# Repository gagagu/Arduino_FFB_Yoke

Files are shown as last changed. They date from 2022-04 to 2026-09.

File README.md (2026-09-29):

# Arduino_FFB_Yoke
Flightsim FFB Yoke with Arduino Leonardo

## see the fork of my project: 
[here](https://github.com/barsk/Arduino_FFB_Yoke)

### use at your own risk. 
I am not responsible for any damage to man and machine. Be careful when handling electronics and mechanics.

### It is not allowed to use my work in a commercial way!
If you want to use it in an commercial way please contact me.

## Please study the [Wiki](https://github.com/gagagu/Arduino_FFB_Yoke/wiki) for more info and before you begin!

## New Hardware and new PCB Verison 2.0
The new Hardware is using an Arduino Pro Micro instead of original Arduino Micro because it's cheaper and easier to order.
The new Hardware created by JR4 is working with the old PCB V1.3.5 and the new PCB V2.0

The new Hardware is available [here](https://www.thingiverse.com/thing:6464701)

I have done some remixed with different planetary gears and other stuff [here](https://www.thingiverse.com/thing:6786283)

For the new Code with automatic calibration switch the branch to "2.0" but be careful, it's in alpha state and I am not responsible for any damage to man and machine. Be careful when handling electronics and mechanics.

To open the Code in Arduino Studio you have to place it into a directory called "Arduino_FFB_Yoke"!

You can use the code with board v2.0 and board v1.3.5 together. You only have to switch in defines.h file.

### This project is still in development and will be extend constantly.

It shows how to create a force feedback yoke (and later pedals) for using with Flight Simulator.
It consist of 3d components, electronic schematics and arduino source code.

## Discord
You are welcome to join my Discord to get newest Info and support, [here](https://discord.gg/zrYUcJWu7F)

## Ref
This project is a combination of several existing github projects and 3d Models from Thingiverse.com

### Github Projects, Thanks a lot for your work!
* [FINO](https://github.com/jmriego/Fino)
* [Heironimus](https://github.com/MHeironimus/ArduinoJoystickLibrary)
* [hoantv](https://github.com/hoantv/VNWheel)
* [YukMingLaw](https://github.com/YukMingLaw/ArduinoJoystickWithFFBLibrary) 
* [arafin](https://github.com/araffin/arduino-robust-serial/)
* [jimmyberg](https://github.com/jimmyberg/LowPassFilter)

### Thingiverse
* [Arduino FFB Yoke 2.0](https://www.thingiverse.com/thing:6464701)
* [Arduino FFB Yoke 2.0 Remixes](https://www.thingiverse.com/thing:6786283)
* [CadetYoke v2.0](https://www.thingiverse.com/thing:4884092)
* [Saitek FFB Yoke](https://www.thingiverse.com/thing:5241628)

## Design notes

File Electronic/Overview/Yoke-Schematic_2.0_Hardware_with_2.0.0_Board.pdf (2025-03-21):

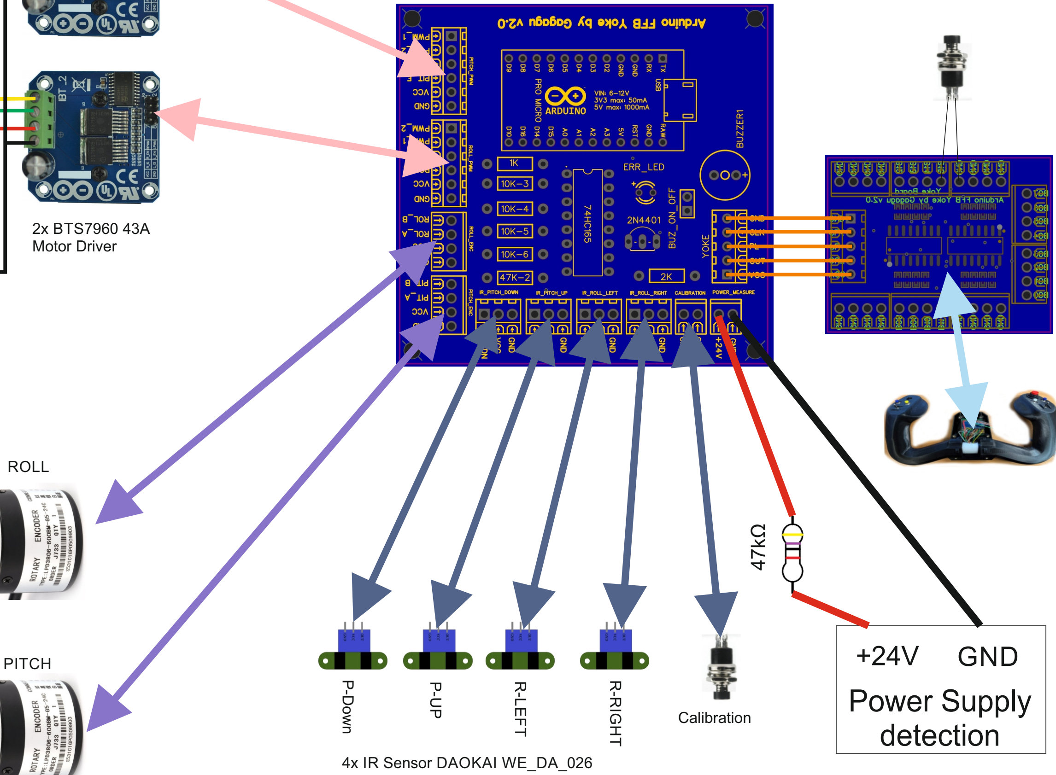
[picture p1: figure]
P-Down; RIG; 4x IR Sensor DAOKAI WE_DA_026; 2x BTS7960 43A Motor Driver; Calibration; ROLL; PITCH; GND; Power Supply detection

Power Supply
24V 10A

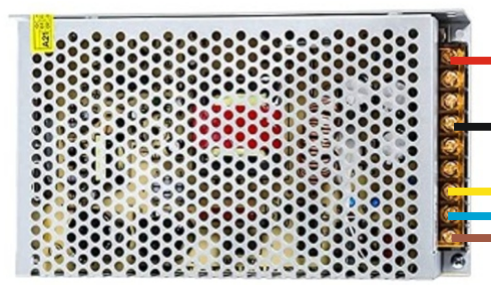
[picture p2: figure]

Power Plug
with Switch

2x 775 DC Motor
12V-36V
3500-900Rpm

# Board v2.0.0 with Hardware 2.0

PITCH

ROLL

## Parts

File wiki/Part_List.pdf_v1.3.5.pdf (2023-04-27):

Partlist Gagagu Arduino FFB Yoke | V1.3 | (prices can change)
Piece | Name | Price Single | Note | Price | Link
1 | Arduino Micro | 19,44 € | | 19,44 € | Link (https://store.arduino.cc/products/arduino-micro)
2 | BTS7960 43A | 15,99 € | Motor Driver Module | 31,98 € | Link (https://www.amazon.de/gp/product/B09FLB44TV)
2 | CD74HC4057 | 8,99 € | Multiplexer | 17,98 € | Link (https://www.amazon.de/gp/product/B07VF14YNG)
2 | 775 DC Motor | 15,59 € | 12V-36V 3500-900Rpm | 31,18 € | Link (https://www.amazon.de/gp/product/B075D85KVV)
10 | WE-DA-026 | 1,52 € | IR Speed Sensor | 15,20 € | Link (https://www.amazon.de/dp/B09TK2H9NY)
1 | HD44780 2004 | 10,00 € | LCD Display 4x20 | 10,00 € | Link (https://www.amazon.de/gp/product/B0822PP3WM)
1 | Power Supply 24V 10A | 25,99 € | | 25,99 € | Link (https://www.amazon.de/gp/product/B09JKJGT4M)
2 | MGN12H | 16,99 € | Linear Guide 200mm | 33,98 € | Link (https://www.amazon.de/gp/product/B093LKT3L9)
2 | HK 2512 | 7,19 € | Ball Bearing 25x32x12 | 14,38 € | Link (https://www.amazon.de/dp/product/B0828XDNJ3)
2 | Aeronaut Shaft Adapter | 5,60 € | No- 712455 | 11,20 € | Link (https://www.amazon.de/gp/product/B013GE06JG)
6 | Button Yoke | 0,40 € | Mini Buttons | 2,40 € | Link (https://www.amazon.de/gp/product/B081TZFZVS)
2 | Switch Yoke | 1,00 € | MTS-123 on-off-on | 2,00 € | Link (https://www.amazon.de/gp/product/B07H5NX4G9)
1 | Button Calibration | 5,99 € | | 5,99 € | Link (https://www.amazon.de/dp/B09BMRDPTN)
1 | Delock USB 2.0 Cable | 7,25 € | 25cm | 7,25 € | Link (https://www.amazon.de/dp/B0754MNQPN)
4 | 20x20L B-Typ Nut6 | 3,28 € | 400mm | 13,12 € | Link (https://www.amazon.de/dp/B09FYFBW1M)
1 | Power Switch | 7,49 € | | 7,49 € | Link (https://www.amazon.de/dp/B01H5MK3OI)
1 | Potentiometer | 6,99 € | 10K | 6,99 € | Link (https://www.amazon.de/gp/product/B0B2ZK6YL6)
1 | Taktile Switche | 10,80 € | 5Way Switch | 10,80 € | Link (https://www.amazon.de/gp/product/B0842K7V2L)
1 | Thread insert | 15,45 € | For Yoke Model | 15,45 € | Link (https://www.amazon.de/gp/product/B09MK3VCYC)
1 | Small Screws | 8,39 € | For Yoke Model | 8,39 € | Link (https://www.amazon.de/gp/product/B093BY1XJJ)
2 | Pushbutton Yoke | 0,50 € | 12mm | 1,00 €
1 | Several Screws, Washers and Nuts | 30,00 € | | 30,00 €
10 | Resistors | 0,25 € | 10K | 2,50 €
1 | Div. Cables | 20,00 € | | 20,00 €
1 | Housing (wood) | 30,00 € | | 30,00 €
1 | Metal Pipe 25mm | 8,00 € | | 8,00 €
1 | ecoPla White | 21,99 € | | 21,99 €
404,70 €

8 | M2.5x8-Screw
10 | M3x10-Screw
8 | M3x12-Screw
4 | M3x14-Screw
8 | M3x16-Screw
20 | M3x20-Screw
4 | M4x20-Screw
8 | M4x25-Screw
1 | M4x35-Screw
8 | M6x20-Screw
12 | M6x25-Screw
6 | M6x30-Screw
4 | M6x50-Screw
50 | M3-Washer
12 | M4-Washer
22 | M6-Washer
22 | M6-Nut
8 | M2.5-Nut
50 | M3-Nut
13 | M4-Nut

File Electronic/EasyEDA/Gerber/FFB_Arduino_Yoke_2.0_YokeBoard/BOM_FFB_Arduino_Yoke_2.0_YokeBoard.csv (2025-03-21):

ID | Name | Designator | Footprint | Quantity | Manufacturer Part | Manufacturer | Supplier | Supplier Part | Price
1 | 10kΩ | R1,R2,R3,R4,R5,R6,R7,R8,R9,R10,R11,R12,R13,R14,R15,R16 | R0603 | 16 | 0603WAF1002T5E | UNI-ROYAL(厚声) | LCSC | C25804 | 0.001
2 | 74HC165D,653 | IC1,IC2 | SOIC-16_L9.9-W3.9-P1.27-LS6.0-BL | 2 | 74HC165D,653 | Nexperia(安世) | LCSC | C5613 | 0.111

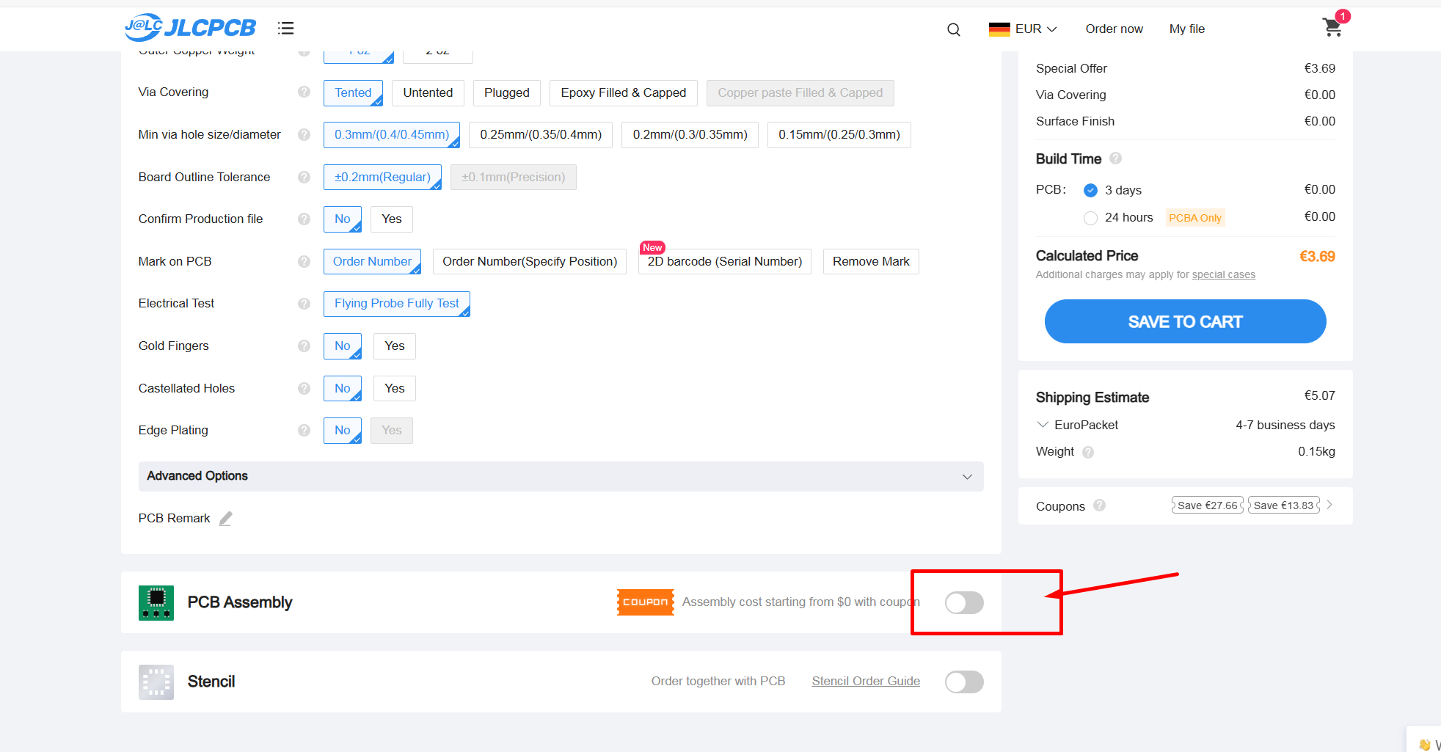
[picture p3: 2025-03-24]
Images/PCB_Order/Order_06.png

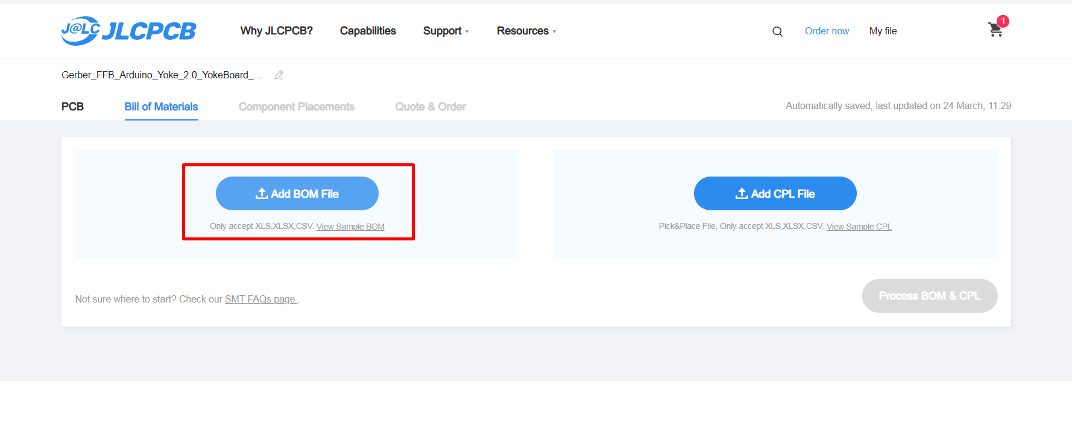
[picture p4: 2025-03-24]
Images/PCB_Order/Order_09.png

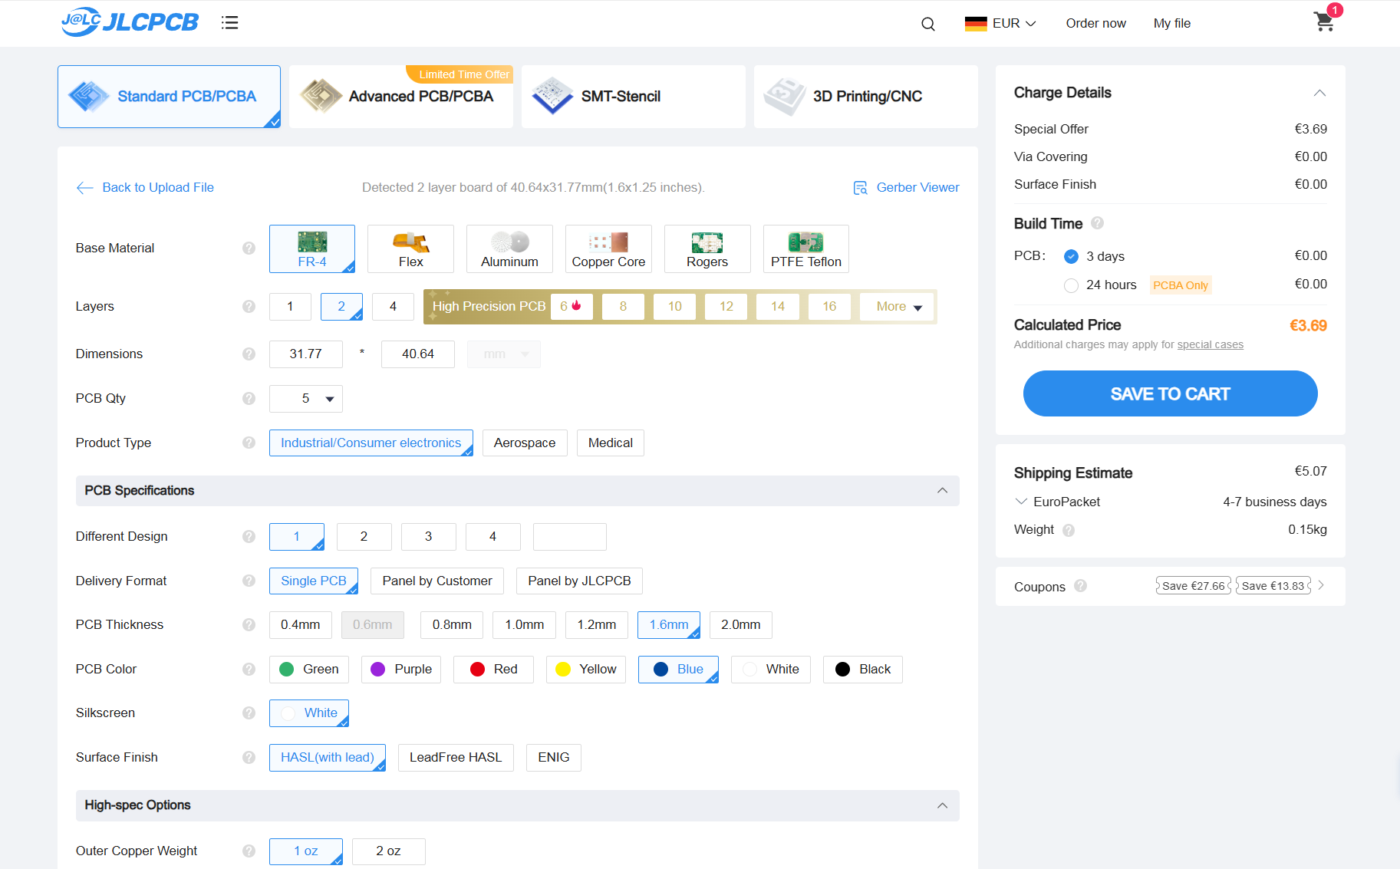
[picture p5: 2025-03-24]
Images/PCB_Order/Order_05.png

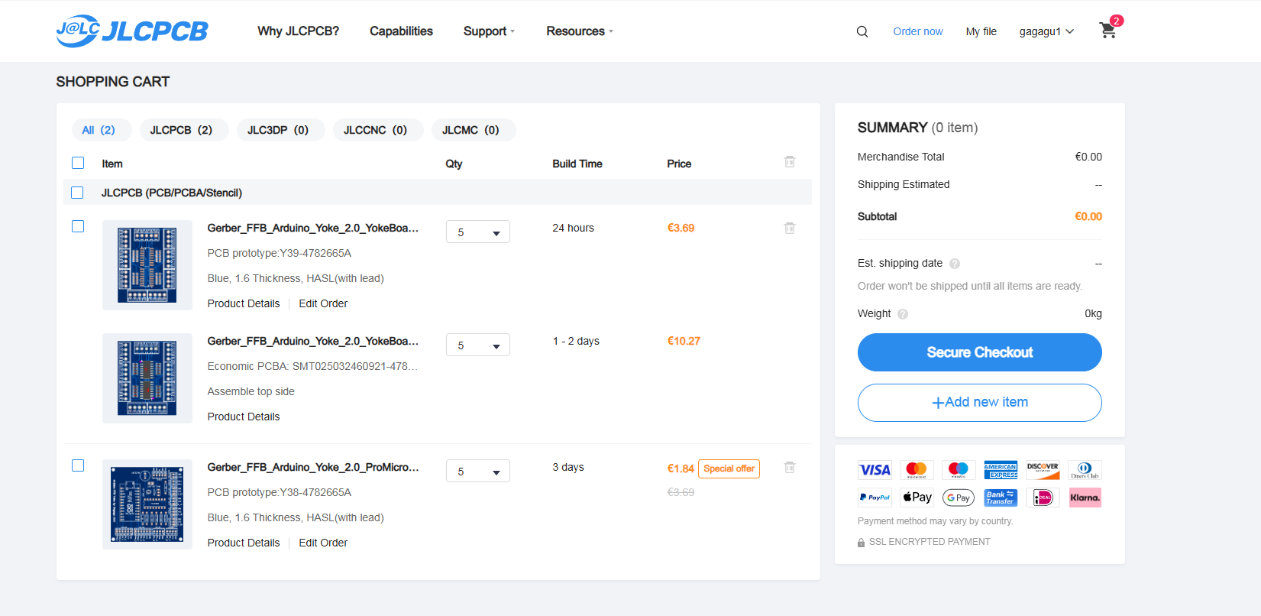
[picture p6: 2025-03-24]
Images/PCB_Order/Order_15.png

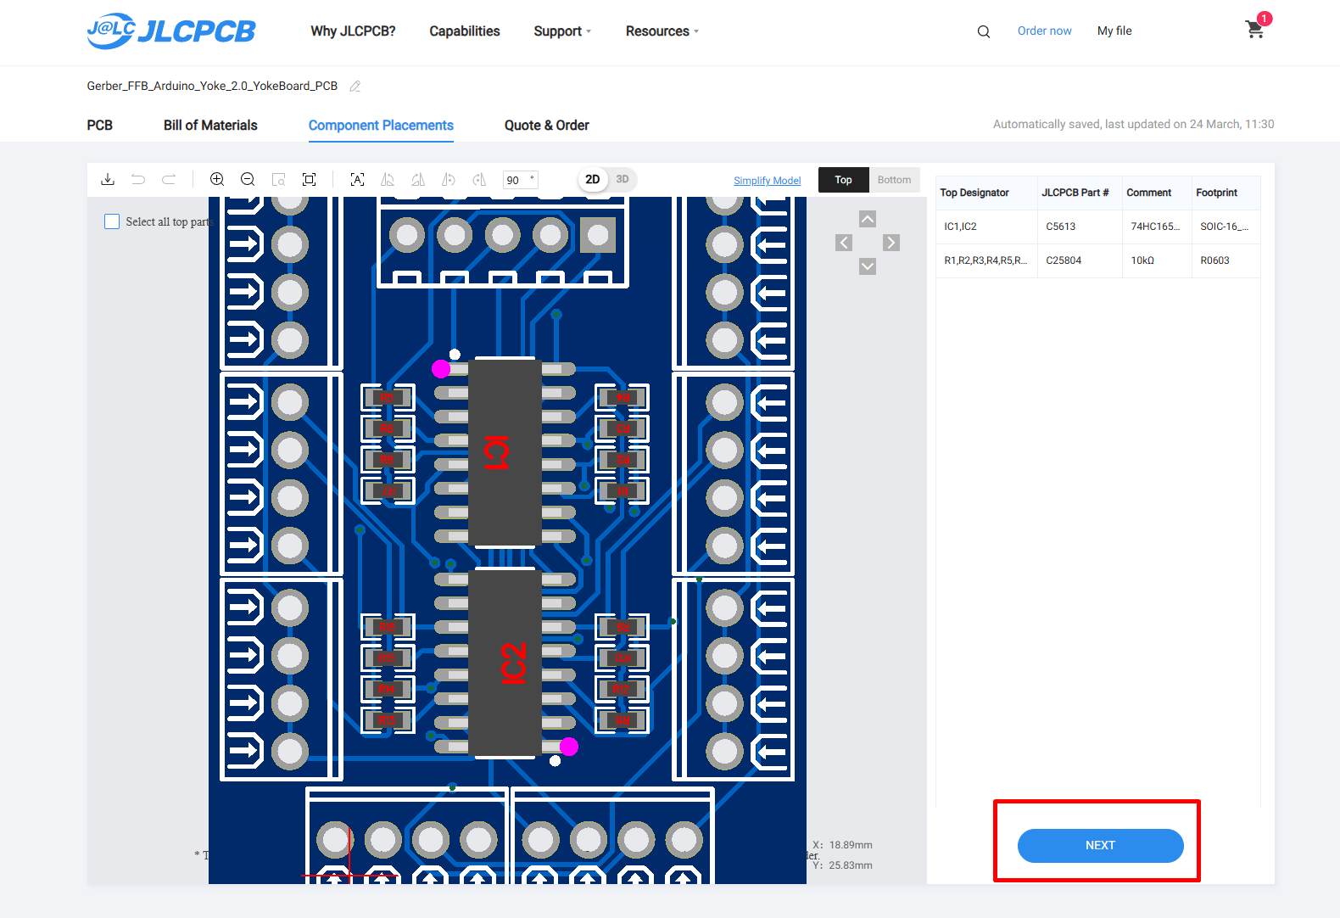
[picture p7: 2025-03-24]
Images/PCB_Order/Order_13.png

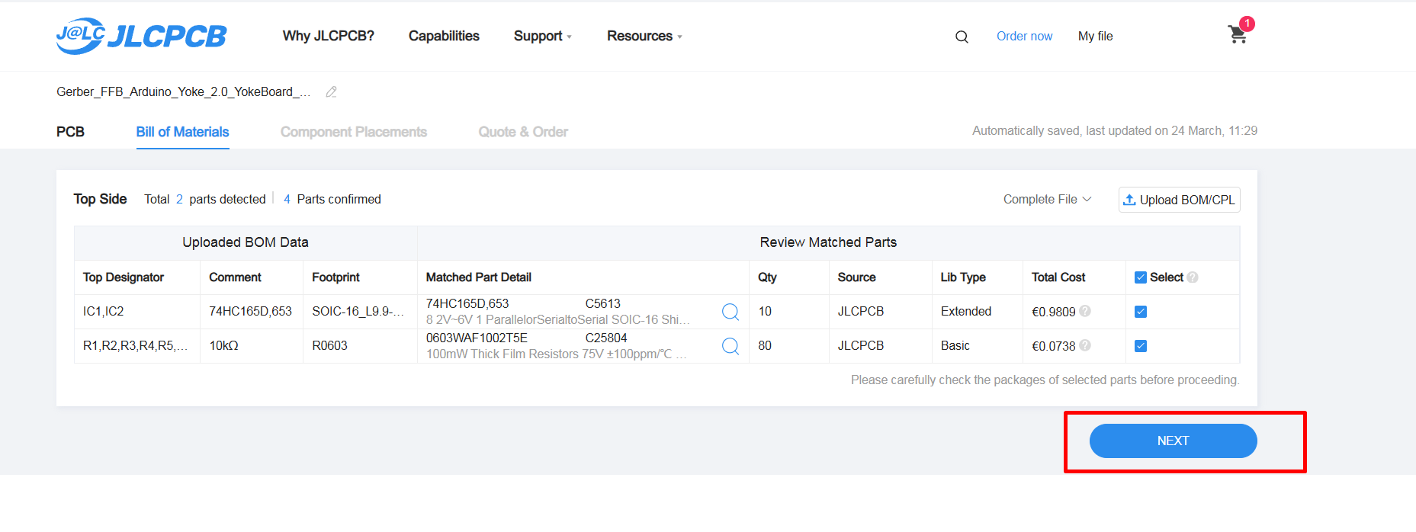
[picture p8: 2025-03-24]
Images/PCB_Order/Order_12.png

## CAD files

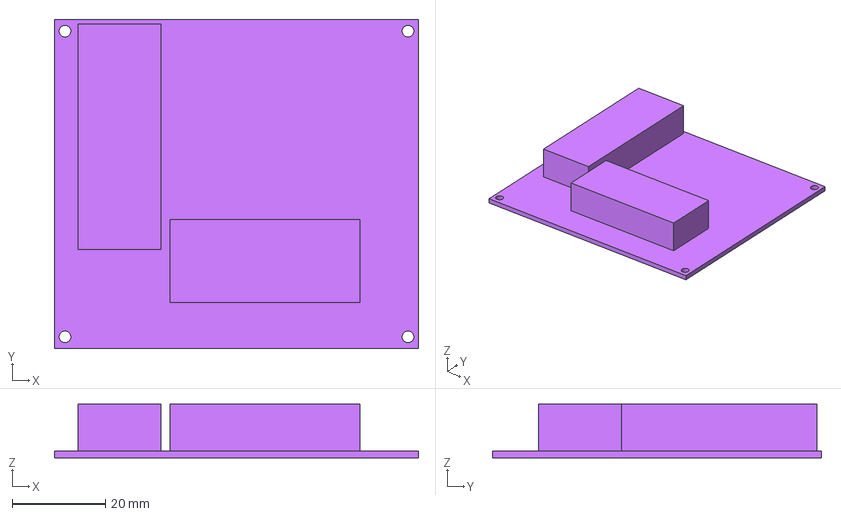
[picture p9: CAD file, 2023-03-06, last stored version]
Cad/FreeCad/Electronics/Mainboard.FCStd
78.0 x 70.5 x 11.5 mm

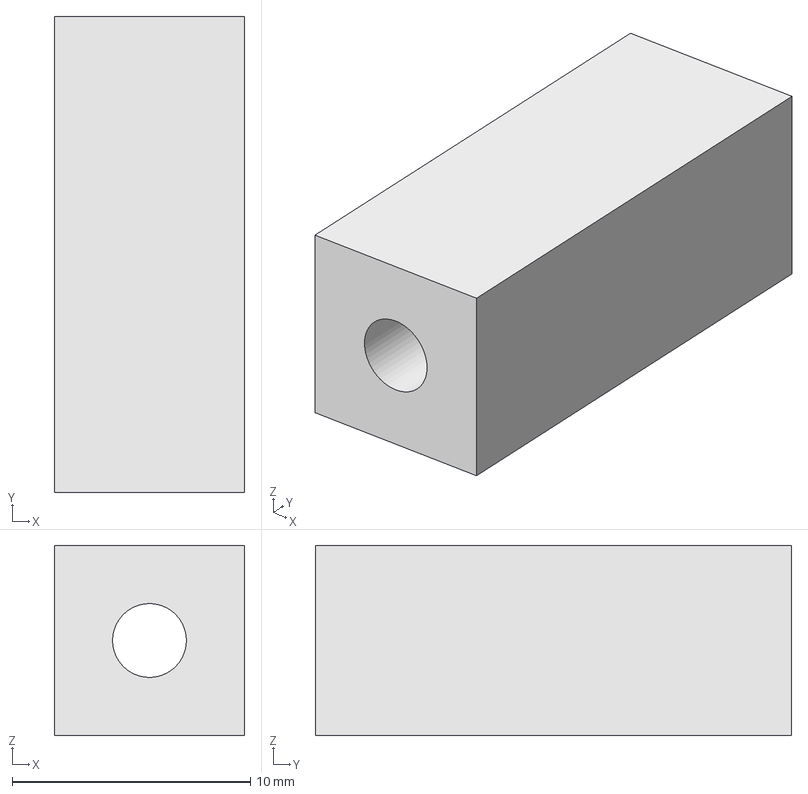
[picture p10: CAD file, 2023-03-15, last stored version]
Cad/FreeCad/Housing/Mainboard_Distance.FCStd
8.00 x 20.0 x 8.00 mm

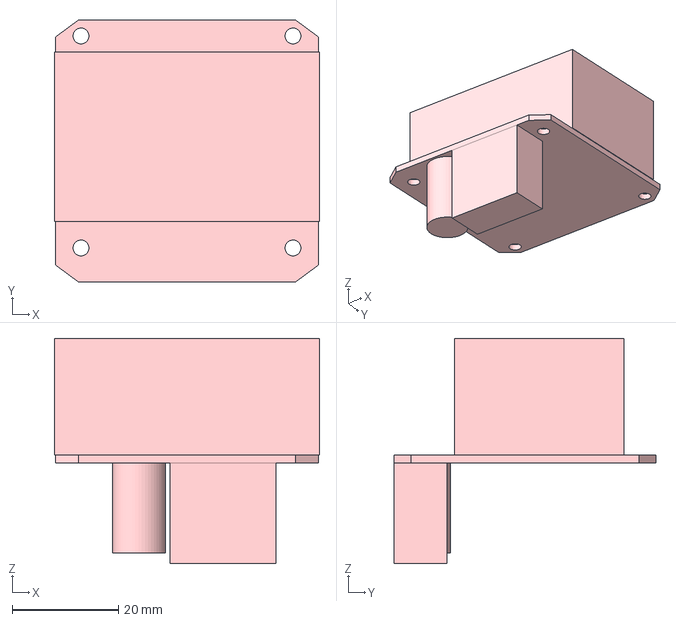
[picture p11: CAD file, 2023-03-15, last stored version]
Cad/FreeCad/Electronics/BTS7960.FCStd
50.0 x 49.4 x 42.5 mm

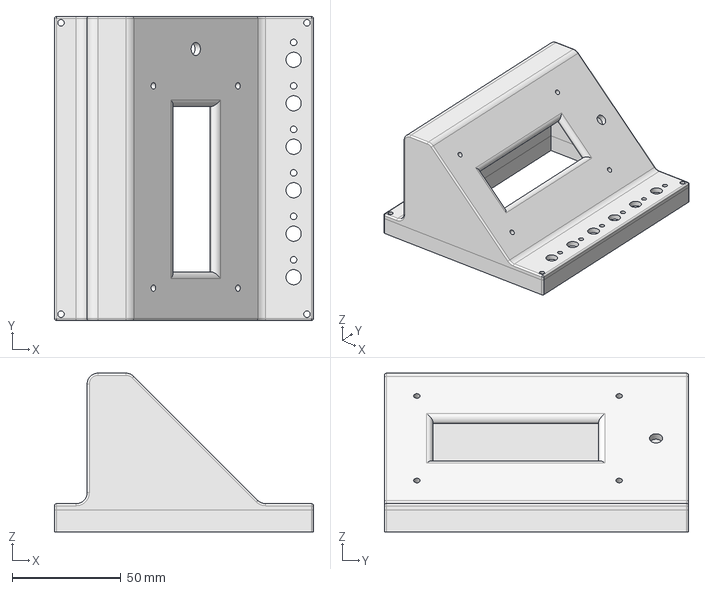
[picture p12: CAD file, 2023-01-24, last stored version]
Cad/FreeCad/Elektronik_V3.FCStd
119.1 x 140.0 x 73.0 mm

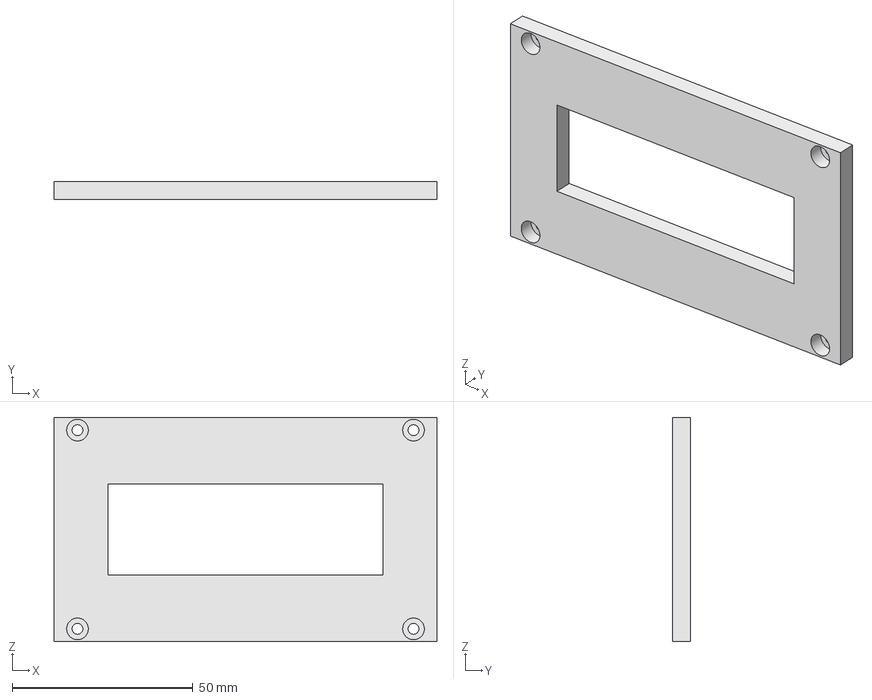
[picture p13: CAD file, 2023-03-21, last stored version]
Cad/FreeCad/Housing/LCD_Cover2.FCStd
106.0 x 5.00 x 62.0 mm

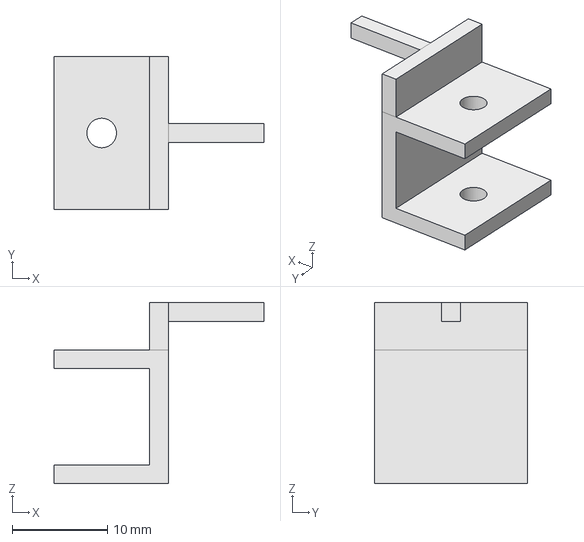
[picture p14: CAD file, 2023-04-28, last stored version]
Cad/FreeCad/IR_Senors_Encoder/IR_Sensor_Pin_Pitch_Center.FCStd
22.0 x 16.0 x 19.0 mm

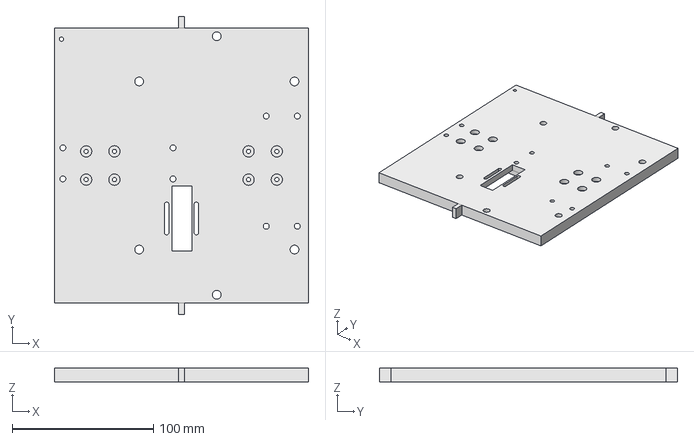
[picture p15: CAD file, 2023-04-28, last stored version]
Cad/FreeCad/Linear_Guide/LinearGuide_Plate.FCStd
180.0 x 211.0 x 10.0 mm

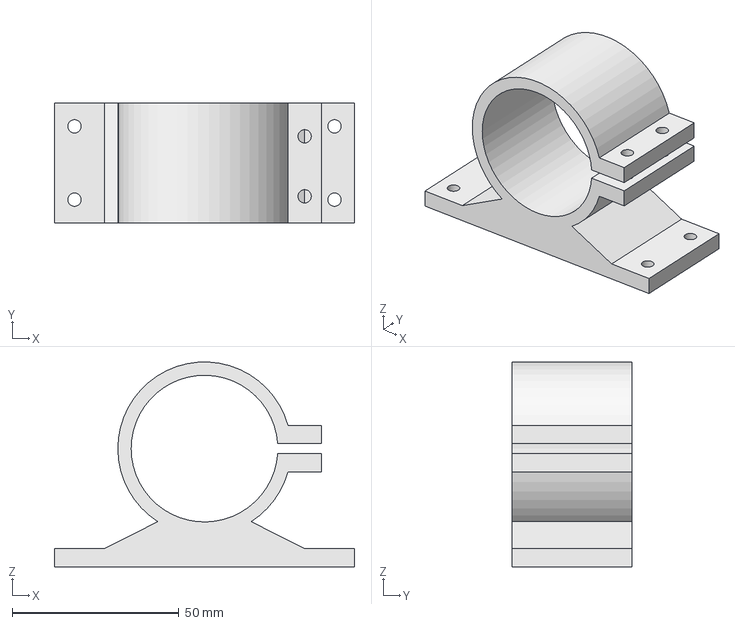
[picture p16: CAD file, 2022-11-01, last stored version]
Cad/FreeCad/Motor/Motor_775_Holder.FCStd
90.0 x 36.0 x 61.5 mm

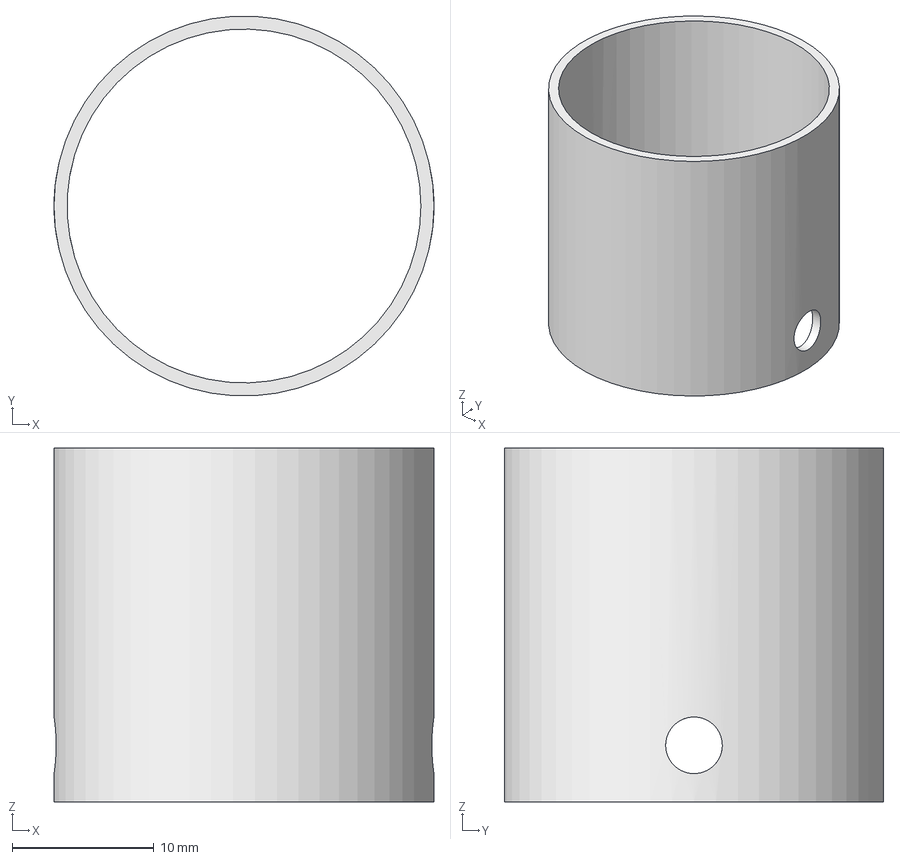
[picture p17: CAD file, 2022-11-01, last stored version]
Cad/FreeCad/Yoke_Model/CadetYoke_Adapter_25mm.FCStd
26.9 x 26.8 x 25.0 mm

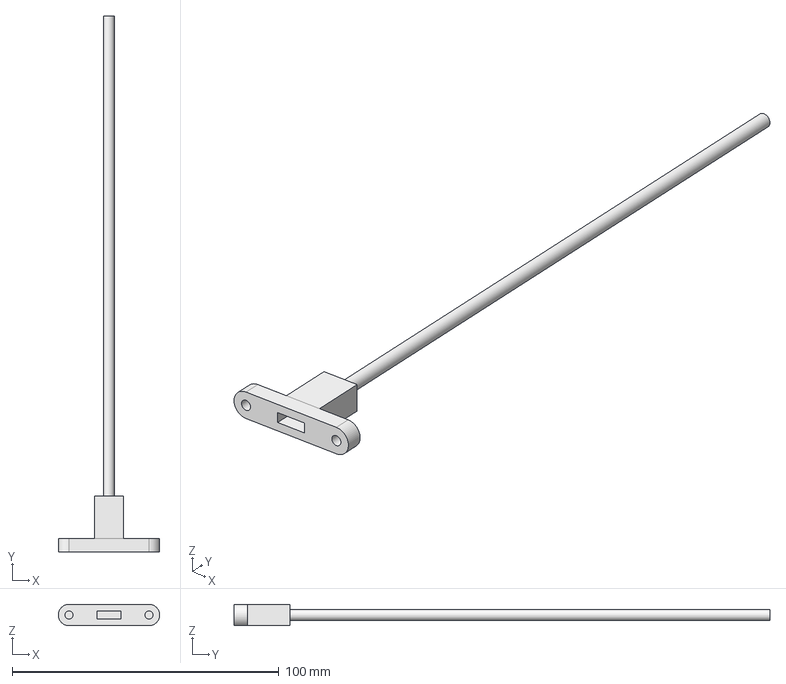
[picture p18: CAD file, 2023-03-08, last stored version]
Cad/FreeCad/Electronics/USB_Connector.FCStd
38.0 x 201.0 x 8.00 mm

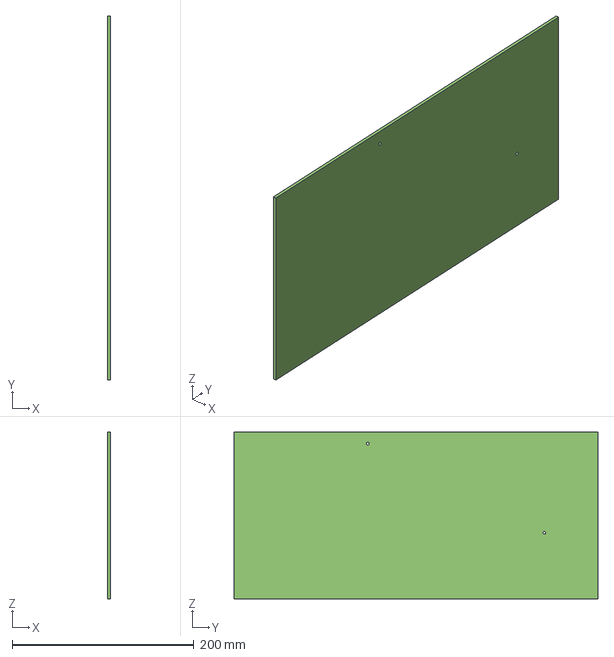
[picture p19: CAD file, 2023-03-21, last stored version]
Cad/FreeCad/Housing/Side_Plate_Right.FCStd
3.00 x 400.0 x 183.0 mm

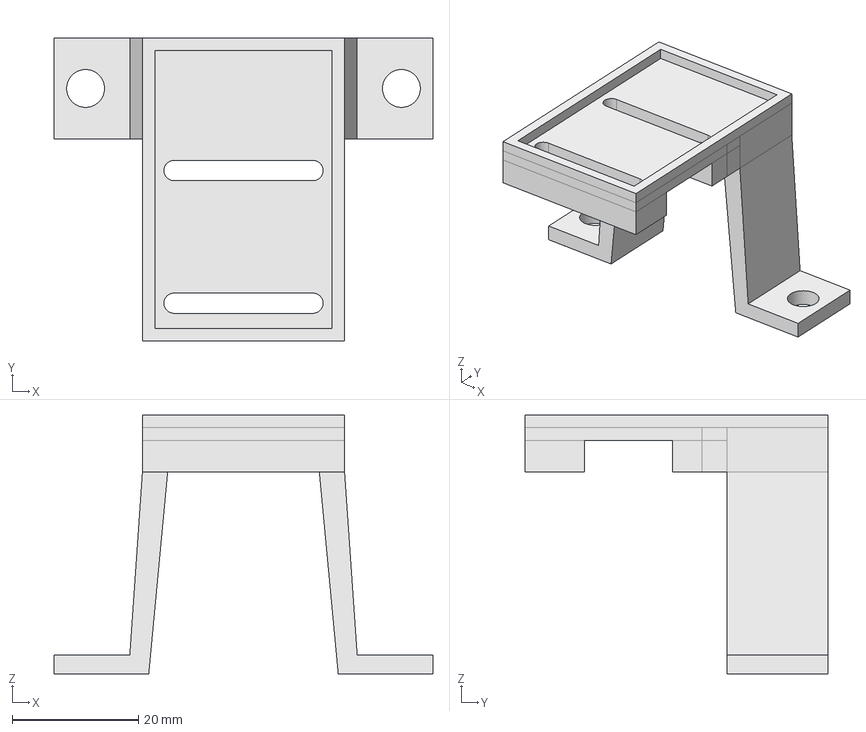
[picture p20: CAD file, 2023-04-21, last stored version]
Cad/FreeCad/IR_Senors_Encoder/IR_Sensor_Holder_Roll_Center.FCStd
60.0 x 48.0 x 41.0 mm

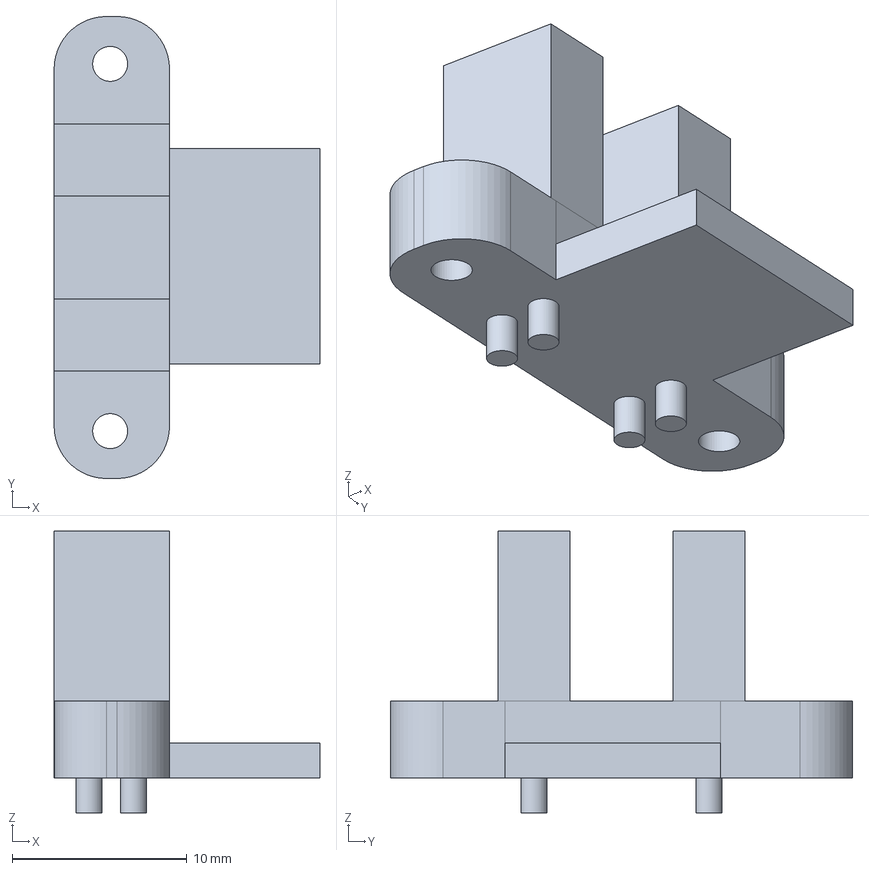
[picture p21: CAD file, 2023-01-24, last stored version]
Cad/FreeCad/IR_Sensor.FCStd
15.2 x 26.4 x 16.1 mm

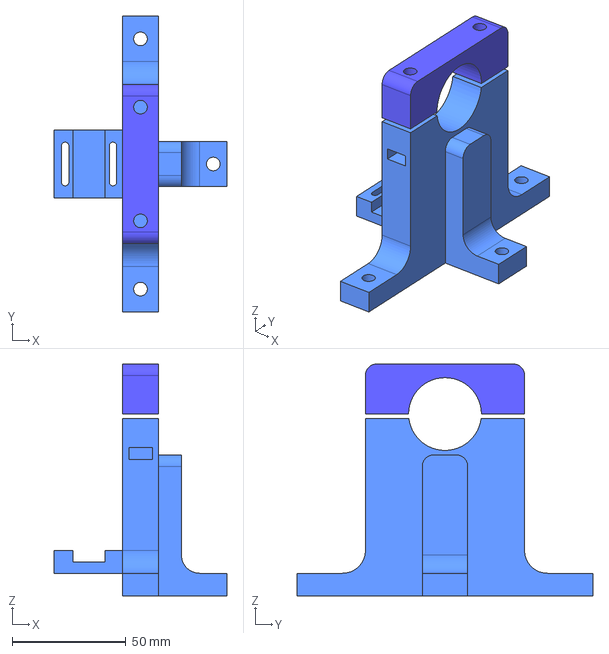
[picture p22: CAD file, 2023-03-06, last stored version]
Cad/FreeCad/Linear_Guide/Bearingblock_Front.FCStd
76.0 x 130.0 x 102.0 mm
Top_Block

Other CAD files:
Cad/FreeCad/Electronics/Power-Connector.FCStd
Cad/FreeCad/Housing/Side_Plate_Left.FCStd
Cad/FreeCad/IR_Senors_Encoder/Yoke_Pipe_EndRing_Sensor.FCStd
Cad/FreeCad/IR_Sensor_Pitch_Endswitch.FCStd
Cad/FreeCad/Backplate.FCStd
Cad/FreeCad/Backplate_2.FCStd
Cad/FreeCad/BallBearing_25mm.FCStd
Cad/FreeCad/Bearingblock.FCStd
Cad/FreeCad/Bottom_Plate.FCStd
Cad/FreeCad/Electronics/LCD_Display.FCStd
Cad/FreeCad/Electronics/Power.FCStd
Cad/FreeCad/Electronics/Switch.FCStd
Cad/FreeCad/Elektronik.FCStd
Cad/FreeCad/Elektronik_V2.FCStd
Cad/FreeCad/Frontplate.FCStd
Cad/FreeCad/Frontplate_2_L.FCStd
Cad/FreeCad/Frontplate_2_R.FCStd
Cad/FreeCad/Housing/Back_Plate.FCStd
Cad/FreeCad/Housing/Back_Plate.dxf
Cad/FreeCad/Housing/Bottom_Plate.FCStd
Cad/FreeCad/Housing/Bottom_Plate.dxf
Cad/FreeCad/Housing/Front_Plate.FCStd
Cad/FreeCad/Housing/Front_Plate.dxf
Cad/FreeCad/Housing/LCD_Cover.FCStd
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

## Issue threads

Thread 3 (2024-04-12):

Updates to descriptions

barsk, 2024-04-12:
Hi looking at your awesome project and greatly impressed. Did you actually implement the FFB protocol forces yourself just by looking through the specs? Really impressive. I have been fiddling a bit with that as well, but I ended up using some other code that was on the net as a basis and then refined that.

The description and specs seem somewhat outdated though as the HW with version 2.0 is s bit different. Would it be possible for you to find some time to update them? I guess some of the 2.0 changes affect electronics and software?

I have a question about the motors, in the 2.0 version a 4:1 gear is used to reduce rpm and increase torque, however why no go a bit further with the gears to get a bit more torque? I guess you do not need that much rpm really? Or?

These motors with attached gears rate from 5 to 600 rpm and are attainable in the EU at reasonable prices. I'm just not sure which motor to choose? [https://www.plexishop.it/en/robotics-and-automation/motors-for-arduino/dc-motors.html](https://www.plexishop.it/en/robotics-and-automation/motors-for-arduino/dc-motors.html)

gagagu, 2024-04-15:
Hi, the FFB Protocol is not created by me. It's based on the Prject called "Fino" (see in Description). This is not the right place to discuss your case and i would invite you to my Discord to discuss it further. See the discord link in the project description, too.

I am working on a Cessna 172 panel, this also includes the implementation of the version 2.0 yoke. By this i will also update the documentation and software.

The newest Version 2.0 is a new hardware design which use the same pcb but instead of using IR Sensors we decided to switch to rotary encoders. The center IR Sensors are also not needed. But some small Code changes are needed to use this version. The changes are very small and not yet uploaded but i can send it to you if you contact me on Discord.

greetings

barsk, 2024-04-18:
Thanks! I will join the Discord server asap. See you there.

1766029053, 2024-04-28:
So happy to have you join this forum

gagagu, 2024-04-30:
Thx

Closed 2024-04-30.

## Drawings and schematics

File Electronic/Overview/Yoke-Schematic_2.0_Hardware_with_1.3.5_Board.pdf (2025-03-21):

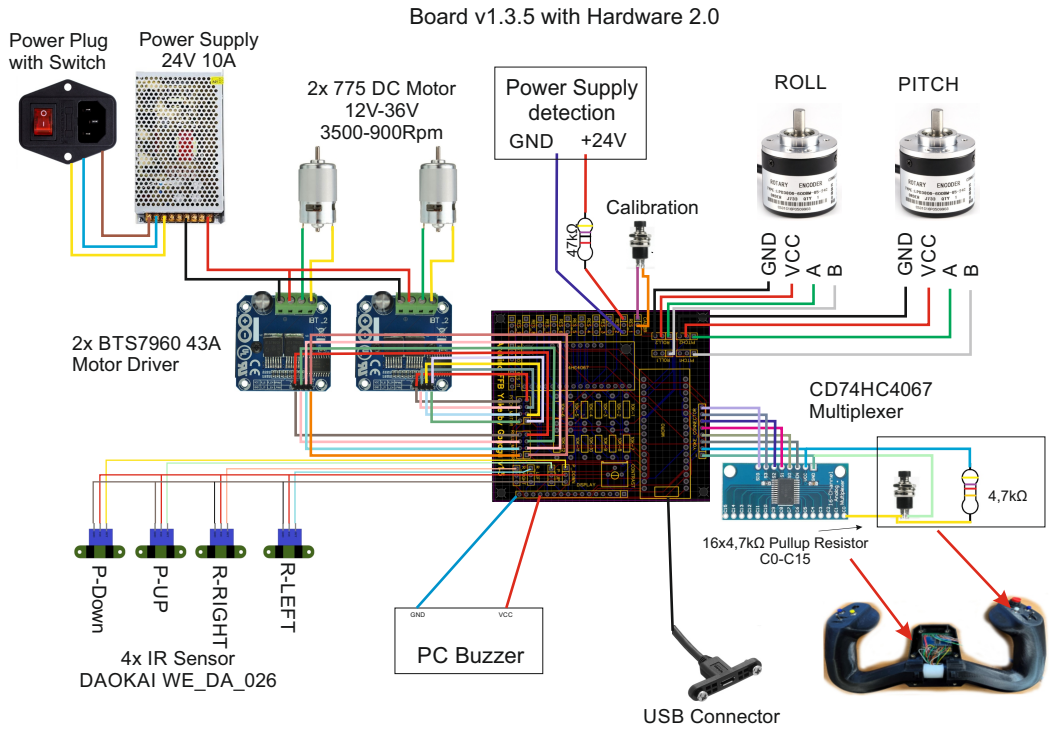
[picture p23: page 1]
P-Down; RIG; 4x IR Sensor DAOKAI WE_DA_026; 2x BTS7960 43A Motor Driver; Power Supply 24V 10A; Power Plug with Switch; 2x 775 DC Motor 12V-36V 3500-900Rpm; Calibration; USB Connector; CD74HC4067 Multiplexer; 16x4,7kΩ Pullup Resistor C0-C15; ROLL; PITCH; GND; Power Supply detection 47kΩ; PC Buzzer; VCC

Board v1.3.5 with Hardware 2.0

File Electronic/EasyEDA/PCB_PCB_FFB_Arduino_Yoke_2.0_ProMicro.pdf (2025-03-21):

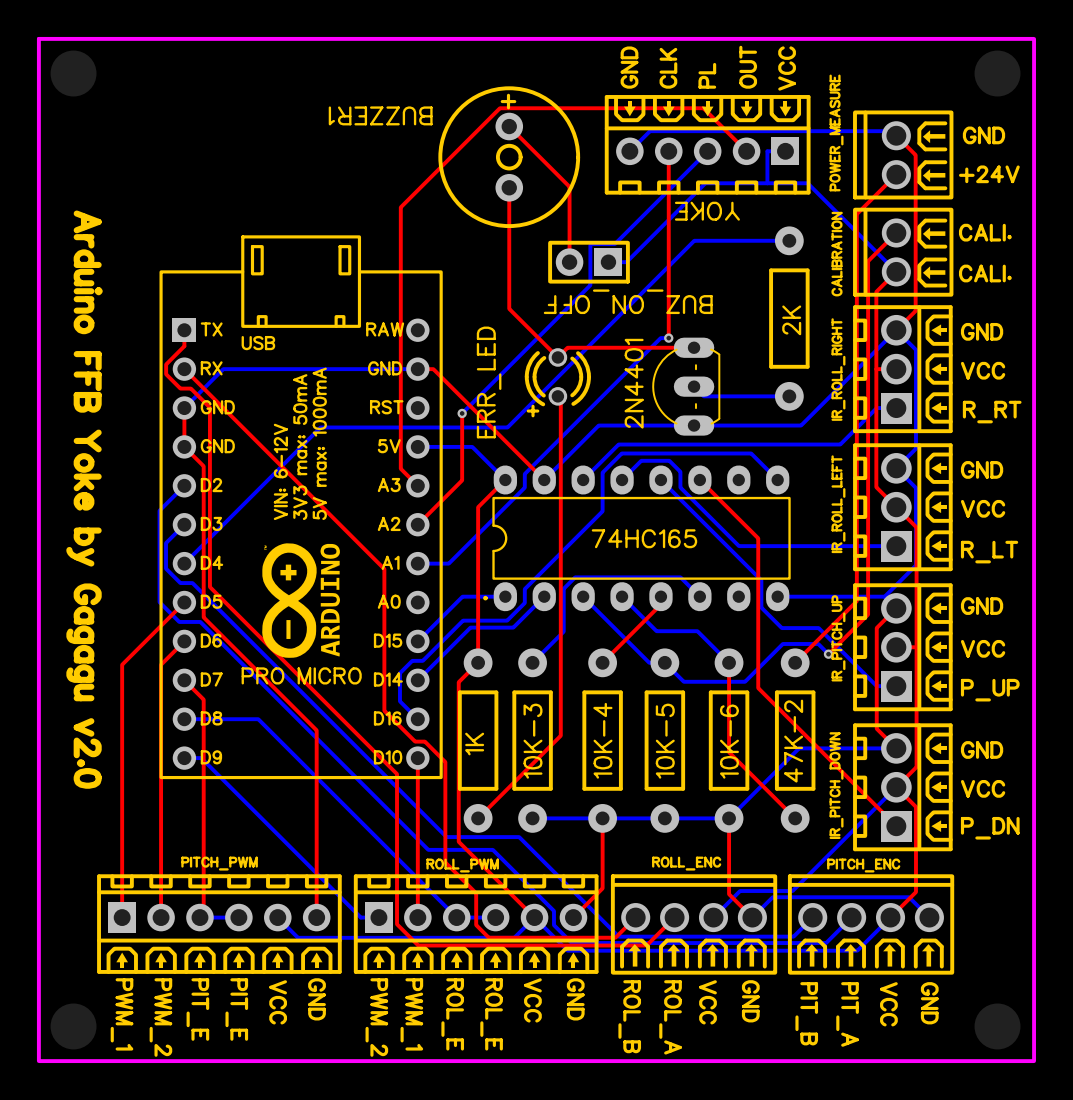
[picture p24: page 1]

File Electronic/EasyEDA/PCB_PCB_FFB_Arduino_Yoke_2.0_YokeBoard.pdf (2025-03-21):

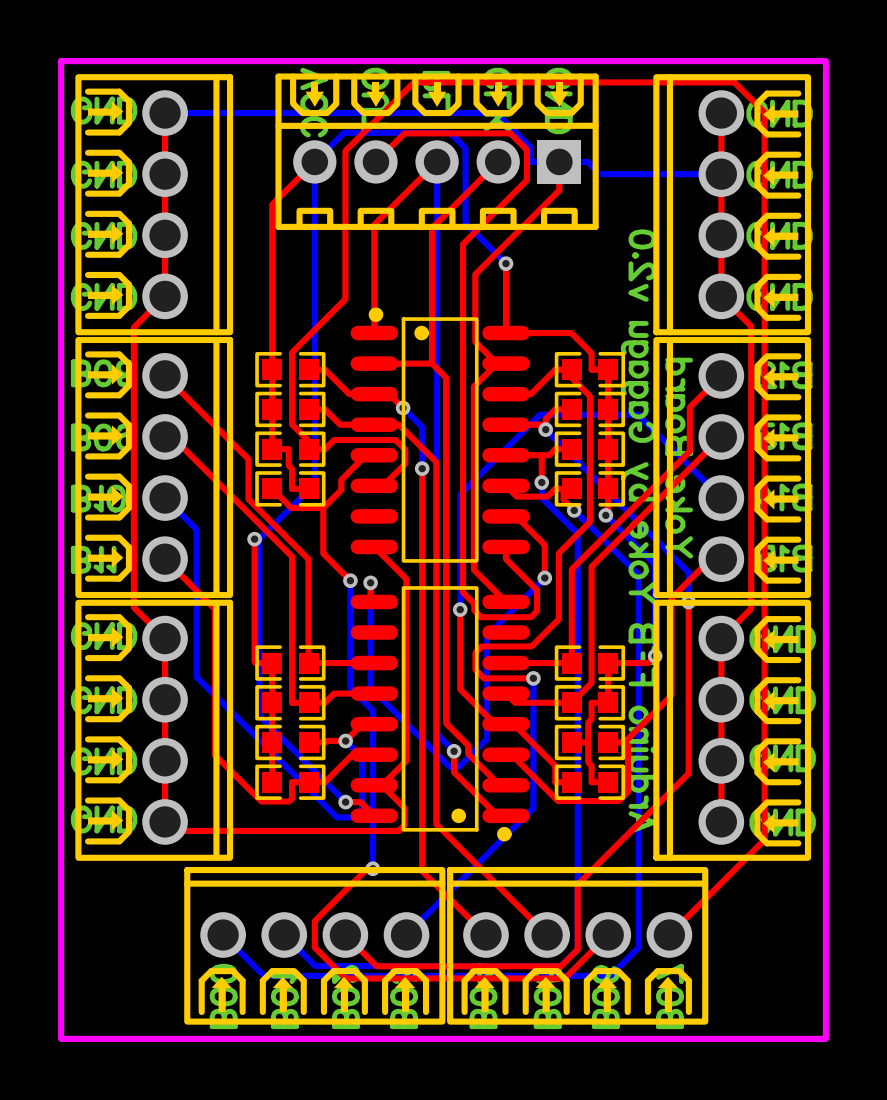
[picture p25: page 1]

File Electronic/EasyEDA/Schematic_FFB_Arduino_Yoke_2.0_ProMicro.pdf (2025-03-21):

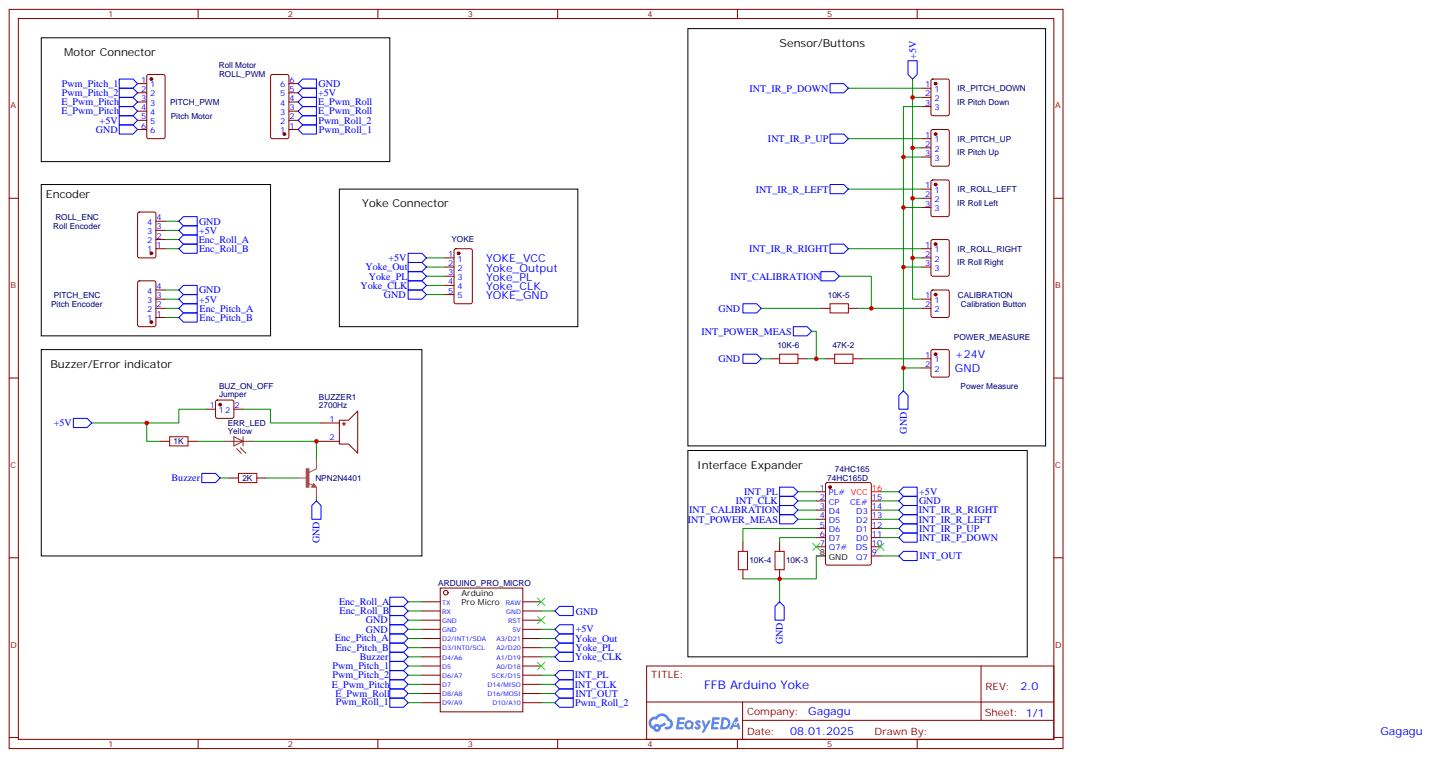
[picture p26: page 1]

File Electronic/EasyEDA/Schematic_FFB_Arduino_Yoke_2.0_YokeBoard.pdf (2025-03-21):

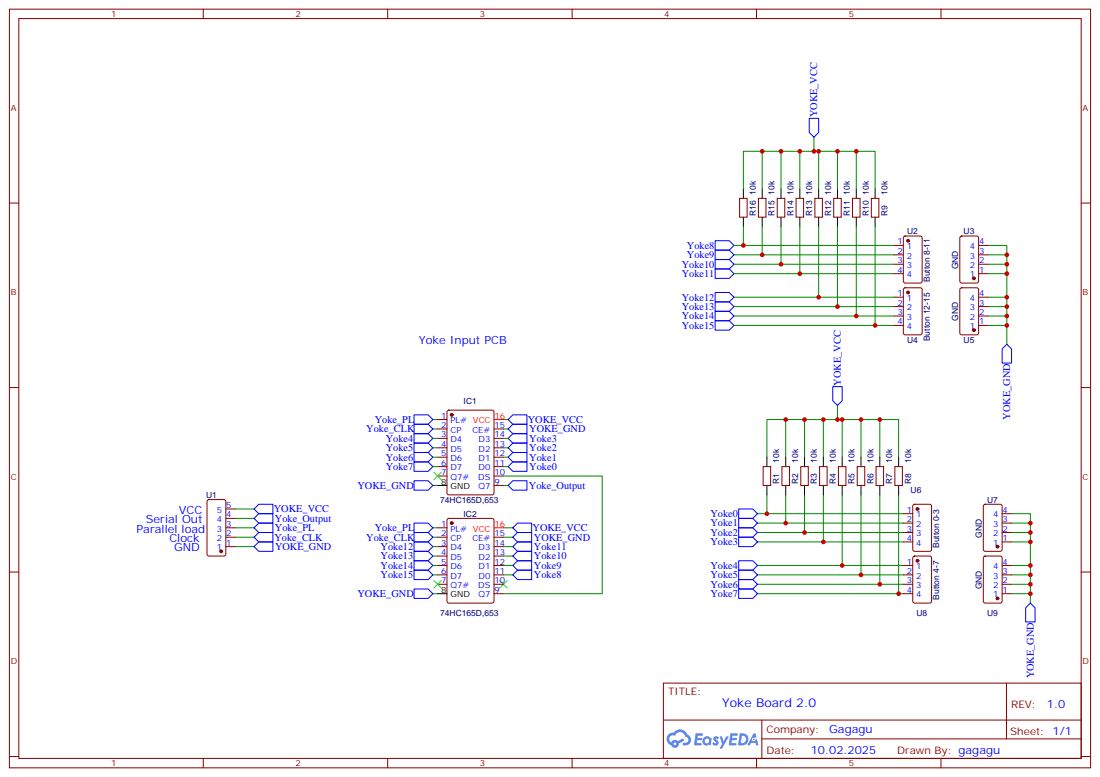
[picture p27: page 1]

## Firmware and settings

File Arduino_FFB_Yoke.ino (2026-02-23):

/*
  Version 2.0.0
*/

/* 
 Created by A.Eckers aka Gagagu
 http://www.gagagu.de
 https://github.com/gagagu/Arduino_FFB_Yoke
 https://www.youtube.com/@gagagu01
*/

/*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
  By using this code, you acknowledge and agree that you are solely responsible for any 
  consequences that may arise from its use. 

  For DIY projects involving electronic and electromechanical moving parts, caution is essential. 
  Ensure that you take the appropriate safety precautions, particularly when working with electricity. 
  Only work with devices if you understand their functionality and potential risks, and always wear 
  appropriate protective equipment. 
  Make sure you are working in a safe, well-lit environment, and that all components are properly installed and secured to avoid injury or damage.

  Special caution is required when building a force feedback device. Unexpected or sudden movements may occur, 
  which could lead to damage to people or other objects. 
  Ensure that all mechanical parts are securely mounted and that the work area is free of obstacles.
  
  By using this project, you acknowledge and agree that you are solely responsible for any consequences that may arise from its use. 
  The author(s) will not be held liable for any damages, injuries, or issues arising from the use of the project, 
  including but not limited to malfunctioning hardware, electrical damage, personal injury, or damage caused by 
  unintended movements of the force feedback device. The responsibility for proper handling, installation, 
  and use of the devices and components lies with the user.
  
  Use at your own risk.
*/

/*
  This is the MAIN FILE and has to be open in an Directory called "Arduino_FFB_Yoke". Otherwise the building of code will not work.
  This version is usable for Hardware v1.3 with Arduino Micro (original) and Hardware v2.0 with Arduino pro Micro
  See the defines.h for pin and cpu definitions definitions
*/
/*************************
  Includes
**************************/
#include "src/Joystick.h"  // Joystick and FFB Library (many changes made) by https://github.com/jmriego/Fino
#include <Encoder.h>       // Encoder Library https://github.com/PaulStoffregen/Encoder
#include <EEPROM.h>        // https://docs.arduino.cc/learn/built-in-libraries/eeprom

#include "defines.h"
#include "Multiplexer.h"
#include "AxisCalibration.h"  // Include the header file
#include "BeepManager.h"

/*************************
  Variables
**************************/
int16_t JOYSTICK_minX = -256;         // initial Joystick axis resolution
int16_t JOYSTICK_maxX = 256;
int16_t JOYSTICK_minY = -256;
int16_t JOYSTICK_maxY = 256;

unsigned long nextJoystickMillis = 0;   // count millis for next joystick update
unsigned long nextEffectsMillis = 0;    // count millis for next Effect update
unsigned long currentMillis;            // millis for the current loop

bool blSerialDebug = false;             // serial debug mode
bool blCalibration = true;              // start flag
byte bSerialIndex = 0;                  // global index for serial communication

int16_t forces[MEM_AXES] = { 0, 0 };        // stored forces
Gains gains[FFB_AXIS_COUNT];                // stored gain parameters
EffectParams effects[MEM_AXES];             // stored effect parameters

int16_t adjForceMax[MEM_AXES] = { 0, 0 };  // stored max adjusted force
byte adjPwmMin[MEM_AXES] = { 0, 0 };       // stored start pwm (motor power) on force != 0
byte adjPwmMax[MEM_AXES] = { 0, 0 };       // stored max pwm (motor power) on max force

Encoder counterRoll(ROLL_ENC_A,ROLL_ENC_B );   // init encoder library for roll ir sensor
Encoder counterPitch(PITCH_ENC_A,PITCH_ENC_B);  // init encoder library for pitch ir sensor

BeepManager beepManager(BUZZER_PIN);  // Instanz der BeepManager Klasse

// variables for Speed calculation
byte roll_speed = 0;
byte pitch_speed = 0;

// variables for calculation
unsigned long lastEffectsUpdate = 0;  // count millis for next effect calculation
int16_t lastX;                        // X value from last loop
int16_t lastY;                        // Y value from last loop
int16_t lastVelX;                     // Velocity X value from last loop
int16_t lastVelY;                     // Velocity y value from last loop
int16_t lastAccelX;                   // Acceleration X value from last loop
int16_t lastAccelY;                   // Acceleration X value from last loop
int32_t counterRollValue = 0;
int32_t counterPitchValue = 0;
bool isCalibrationPressed = false;   // flag for calibration button

Joystick_ Joystick(            // define Joystick parameters
  JOYSTICK_DEFAULT_REPORT_ID,  // ID defined in Joystick.h
  JOYSTICK_TYPE_JOYSTICK,      // type Joystick
  12, 1,                       // Button Count, Hat Switch Count
  true, true, false,           // X, Y, Z
  false, false, false,         // Rx, Ry, Rz
  false, false);               // rudder, throttle

Multiplexer mux(&Joystick);   // class for mutiplexers

Axis rollAxis(ROLL_L_PWM, ROLL_R_PWM, true, &counterRoll, &mux, &beepManager);        // Roll Axis class
Axis pitchAxis(PITCH_U_PWM, PITCH_D_PWM, false, &counterPitch, &mux, &beepManager);   // pitch axis class

/********************************
     initial setup
*******************************/
void setup() {
  ArduinoSetup();   // setup for Arduino itself (pins)
  SetupJoystick();  // Joystick setup

  Serial.begin(SERIAL_BAUD);  // init serial

  // if serial debig, no motors enabled
#ifndef SERIAL_DEBUG
   EnableMotors();             // enable motors
#endif

   delay(1000);
   beepManager.SystemStart();  // Systemstart-Sound
}  //setup


/***************************
      main loop
****************************/
void loop() {

// if serial debug mode than only display pins, mux and counters
#ifdef SERIAL_DEBUG
  mux.ReadMux();                // read ir sensors
  mux.UpdateJoystickButtons();  // read yoke buttons
  Serial.print(", Roll:");      
  Serial.print(counterRollValue);
  Serial.print(", Pitch:");
  Serial.print(counterPitchValue);  
  //if calibration button is pressed than reset counters
  if (mux.CalibrationButtonPushed()) {  
    counterRoll.readAndReset(); 
    counterPitch.readAndReset();
  }
  Serial.println("");
  delay(30);
#else
// else normal yoke mode

  currentMillis = millis();   // number of milliseconds passed since the Arduino board began running the current program

  counterRollValue=counterRoll.read();
  counterPitchValue=counterPitch.read();
  mux.ReadMux();              // Read values of buttons and end switch sensors (except yoke axes)

  if (blCalibration) {        // calibration should start?
    Calibrate();
    blCalibration = false;
  } else {
    // prevent double start calibration and missing the button press
    if (mux.CalibrationButtonPushed()) {  
      isCalibrationPressed = true;
    } else {
      if (isCalibrationPressed == true) {
        isCalibrationPressed = false;
        blCalibration = true;
      }
    }

    // normal yoke mode
    if (currentMillis >= nextJoystickMillis) {  // do not run more frequently than these many milliseconds, the window system needs time to process
      mux.UpdateJoystickButtons();              // set Joystick buttons
      Joystick.sendState();                     // send joystick values to system

      if (currentMillis >= nextEffectsMillis) {   // we calculate condition forces every 100ms or more frequently if we get position updates
        UpdateEffects(true);                      // update/calculate new effect paraeters
        nextEffectsMillis = currentMillis + 100;  // set time for new effect loop
      } else {
        UpdateEffects(false);  // calculate forces without recalculating condition forces
                               //this helps having smoother spring/damper/friction
                               //if our update rate matches our input device
      }                        //nextEffectsMillis  || pos_updated

      if (mux.MotorPower()) {
        PrepareMotors();
      }                                         // move motors
      nextJoystickMillis = currentMillis + 20;  // set time for new joystick loop

      SerialEvent();                                                  // check if serial event received
    }  //nextJoystickMillis
  }    // else
#endif
}  // loop


/***************************
  Calibration
****************************/
void Calibrate() {
  delay(1000);

  // check motor power available
  if (!mux.MotorPower()) {               // is motor power available?
    beepManager.CalibrationError();  //  Calibration error beep
    delay(BEEP_CODE_DELAY);
    beepManager.NoMotorPower();
    return;
  }

  beepManager.CalibrationStart();  // Calibration start beep
  delay(BEEP_CODE_DELAY);

  // Start ROLL axis calibration
  rollAxis.Calibrate();     
  // check error
  if(rollAxis.CheckError(true))
  {
    return;
  }

  delay(500);

  // Start PITCH axis calibration
  pitchAxis.Calibrate();
  // check error
  if(pitchAxis.CheckError(false))
  {
    return;
  }

  SetRangeJoystick();  // Set Joystick range

  
}

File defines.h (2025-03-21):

/* 
 Created by A.Eckers aka Gagagu
 http://www.gagagu.de
 https://github.com/gagagu/Arduino_FFB_Yoke
 https://www.youtube.com/@gagagu01
*/

/*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
  By using this code, you acknowledge and agree that you are solely responsible for any 
  consequences that may arise from its use. 

  For DIY projects involving electronic and electromechanical moving parts, caution is essential. 
  Ensure that you take the appropriate safety precautions, particularly when working with electricity. 
  Only work with devices if you understand their functionality and potential risks, and always wear 
  appropriate protective equipment. 
  Make sure you are working in a safe, well-lit environment, and that all components are properly installed and secured to avoid injury or damage.

  Special caution is required when building a force feedback device. Unexpected or sudden movements may occur, 
  which could lead to damage to people or other objects. 
  Ensure that all mechanical parts are securely mounted and that the work area is free of obstacles.
  
  By using this project, you acknowledge and agree that you are solely responsible for any consequences that may arise from its use. 
  The author(s) will not be held liable for any damages, injuries, or issues arising from the use of the project, 
  including but not limited to malfunctioning hardware, electrical damage, personal injury, or damage caused by 
  unintended movements of the force feedback device. The responsibility for proper handling, installation, 
  and use of the devices and components lies with the user.
  
  Use at your own risk.
*/

#ifndef DEFINES_H
#define DEFINES_H

/*****************************
 uncomment for Serial Debug, only Sensor Data will be write to Serial Monitor
*****************************/
//#define SERIAL_DEBUG 1

/*****************************
 -uncomment for Ardunio Pro Micro
 -comment out for Arduino Micro (original)
*****************************/
#define ARDUINO_PRO_MICRO 1


#define SERIAL_BAUD 115200  // Communication Speed

#ifdef ARDUINO_PRO_MICRO
  #define BUZZER_PIN 4
#else
  #define BUZZER_PIN 12
#endif

// Roll Encoder Pins
#define ROLL_ENC_A 0
#define ROLL_ENC_B 1

// Pitch Encoder Pins
#define PITCH_ENC_A 3
#define PITCH_ENC_B 2

#ifdef ARDUINO_PRO_MICRO
  // Pitch Motordriver pins
  #define PITCH_EN 7
  #define PITCH_U_PWM 5
  #define PITCH_D_PWM 6
#else
  // Pitch Motordriver pins
  #define PITCH_EN 11
  #define PITCH_U_PWM 6
  #define PITCH_D_PWM 13
#endif

// Roll Motordriver pins
#define ROLL_EN 8
#define ROLL_R_PWM 9
#define ROLL_L_PWM 10


  //ARDUINO_PRO_MICRO
  // Multiplexer Yoke Buttons
  #define MUX_YOKE_OUT A3
  #define MUX_YOKE_PL A2
  #define MUX_YOKE_CLK A1

  // Multiplexer Calibration Button, Power Measure, IR Sensors
  #define MUX_INT_OUT 16
  #define MUX_INT_PL 15
  #define MUX_INT_CLK 14

  // for RoxMux Library
  // used for array sizes not pins!
  #define MUX_TOTAL_INT 1
  #define MUX_TOTAL_YOKE 2

  // Arduino Micro 
  // multiplexer for buttons
  #define MUX_S0 A0
  #define MUX_S1 A1
  #define MUX_S2 A2
  #define MUX_S3 A3

  // Multiplexer Yoke Buttons
  #define MUX_EN_YOKE 5
  #define MUX_SIGNAL_YOKE A5

  // Multiplexer Adjustemts for Calib Button, Force Potis, End Switches
  #define MUX_EN_INPUT 4
  #define MUX_SIGNAL_INPUT A4



/*****************************
  Memory array positions for Effects
****************************/
#define MEM_ROLL  0
#define MEM_PITCH  1
#define MEM_AXES  2

// Adjustments array positions
#define ADJ_ENDSWITCH_PITCH_DOWN 0
#define ADJ_ENDSWITCH_PITCH_UP 1
#define ADJ_ENDSWITCH_ROLL_LEFT 2
#define ADJ_ENDSWITCH_ROLL_RIGHT 3
#define ADJ_CALIBRATION_BUTTON 4
#define ADJ_MOTOR_POWER 5


/******************************************
   Communication Command Constants
*******************************************/
//Debug
#define SERIAL_CMD_DEBUG_START 1
#define SERIAL_CMD_DEBUG_STOP 2
#define SERIAL_CMD_DEBUG_STATUS 3
#define SERIAL_CMD_DEBUG_VALUES 4

#define SERIAL_CMD_DEBUG_FORCE_VALUES 8


// read
#define SERIAL_CMD_READ_ALL_PARAMS 10
#define SERIAL_CMD_READ_ALL_VALUES 20

// Write Roll
#define SERIAL_CDM_WRITE_ROLL_FORCE_MAX 101
#define SERIAL_CDM_WRITE_ROLL_PWM_MIN 102
#define SERIAL_CDM_WRITE_ROLL_PWM_MAX 103

#define SERIAL_CDM_WRITE_ROLL_FRICTION_MAX_POSITION_CHANGE 104
#define SERIAL_CDM_WRITE_ROLL_INERTIA_MAX_ACCELERATION 105
#define SERIAL_CDM_WRITE_ROLL_DAMPER_MAX_VELOCITY 106

#define SERIAL_CDM_WRITE_ROLL_TOTAL_GAIN 107
#define SERIAL_CDM_WRITE_ROLL_CONSTANT_GAIN 108
#define SERIAL_CDM_WRITE_ROLL_RAMP_GAIN 109
#define SERIAL_CDM_WRITE_ROLL_SQUARE_GAIN 110
#define SERIAL_CDM_WRITE_ROLL_SINE_GAIN 111
#define SERIAL_CDM_WRITE_ROLL_TRIANGLE_GAIN 112
#define SERIAL_CDM_WRITE_ROLL_SAWTOOTH_DOWN_GAIN 113
#define SERIAL_CDM_WRITE_ROLL_SAWTOOTH_UP_GAIN 114
#define SERIAL_CDM_WRITE_ROLL_SPRING_GAIN 115
#define SERIAL_CDM_WRITE_ROLL_DAMPER_GAIN 116
#define SERIAL_CDM_WRITE_ROLL_INERTIA_GAIN 117
#define SERIAL_CDM_WRITE_ROLL_FRICTION_GAIN 118
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

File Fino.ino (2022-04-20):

#define NODEBUG
#define COMINO
#ifdef _VARIANT_ARDUINO_DUE_X_
#define Serial SerialUSB
#endif

// the digits mean Mmmmrrr (M=Major,m=minor,r=revision)
#define SKETCH_VERSION 3000001

#include "src/Joystick.h"
#include "config.h"
#include "order.h"

// -------------------------
// Various global variables
// -------------------------
unsigned long lastEffectsUpdate;
unsigned long nextJoystickMillis;
unsigned long nextEffectsMillis;

// --------------------------
// Joystick related variables
// --------------------------
#define minX -32768
#define maxX 32767
#define minY -32768
#define maxY 32767

bool is_connected = false;
bool forces_requested = false;
bool pos_updated = false;

int16_t pos[2] = {0, 0};
int lastX;
int lastY;
int lastVelX;
int lastVelY;
int lastAccelX;
int lastAccelY;

EffectParams effects[2];
int32_t forces[2] = {0, 0};

Joystick_ Joystick(
    JOYSTICK_DEFAULT_REPORT_ID, JOYSTICK_TYPE_JOYSTICK,
    19, 2, // Button Count, Hat Switch Count
    true, true, false, // X, Y, Z
    false, false, false, // Rx, Ry, Rz
    true, true); // rudder, throttle

void setup() {

    ArduinoSetup();
    setupJoystick();

    // setup communication
    #if defined(COMINO) || defined(DEBUG)
    Serial.begin(SERIAL_BAUD);
    #endif

    // setup timing and run them as soon as possible
    lastEffectsUpdate = 0;
    nextJoystickMillis = 0;
    nextEffectsMillis = 0;
}

void loop(){
    ReadPots();

    #ifdef COMINO
    get_messages_from_serial();
    #endif

    unsigned long currentMillis;
    currentMillis = millis();
    // do not run more frequently than these many milliseconds
    if (currentMillis >= nextJoystickMillis) {
        updateJoystickPos();
        nextJoystickMillis = currentMillis + 2;

        // we calculate condition forces every 100ms or more frequently if we get position updates
        if (currentMillis >= nextEffectsMillis || pos_updated) {
            updateEffects(true);
            nextEffectsMillis = currentMillis + 100;
            pos_updated = false;
        } else {
            // calculate forces without recalculating condition forces
            // this helps having smoother spring/damper/friction
            // if our update rate matches our input device
            updateEffects(false);
        }

        #ifdef COMINO
        if (forces_requested) {
            sendForces();
            forces_requested = false;
        }
        #endif
    }

    DriveMotors();
}

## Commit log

2022-04-20 update Arduino Code
2022-05-17 Rollback because unknown error.
    [Arduino.ino, Arduino_FFB_Yoke.ino, Joystick.h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]
2022-05-23 do pwm stuff
2022-05-24 setup Pitch Hardware
2022-06-01 Cleanup code and fix the pitch motor control
    [Arduino.ino, Arduino_FFB_Yoke.ino, joystick.ino]
2022-06-01 Pitch Tuning and Fixes
    [Arduino.ino]
2022-06-02 Updated Schematic
2022-06-17 fist button tests, not finished
2022-06-18 Update Schematics.jpg
    Wrong Button assignment.
2022-06-18 Update Arduino.ino
    All Buttons are working now.
2022-06-18 pitch end switch implementation
    Add End Switch for pitch to reduce force on end position
2022-07-08 Update Screenshot_4.jpg
    Update Bearingblock Bottom for Microswitch Endswitches
2022-07-19 Update Arduino.ino
    Add Endswitch for Roll Axe
2022-07-26 Update Schematics.jpg
    Add capacitors for potentiometers
2022-08-07 Fix strange motordriver behavior
    [Arduino.ino, Arduino_FFB_Yoke.ino]
2022-08-09 Insert Calibration for Potis
    Hardware change needed
2022-08-09 Insert calibration Button/LED
2022-08-30 Remove calibration routine
2022-10-05 Switch Pins
    * Switch Pin 11 with 13 and 3 with 6
    * code cleanup
    * change pwm timers
2022-10-17 Code & Electronic redesign
    Complete redesign of code and electonics
    [Arduino.ino, Arduino_FFB_Yoke.ino, Joystick.cpp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]
2022-10-17 update schematic
2022-10-24 Hardware changes
    Insert 20x4 LCD Display
2022-10-25 Upload CAD Sources
    [Backplate.FCStd, Backplate_2.FCStd, BallBearing_25mm.FCStd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]
2022-10-25 PCB Files
    [FFB_Arduino_Yoke_1.0_Leonardo.fzz]
2022-12-01 Update Schemarics and PCB
2022-12-01 Update Fritzing Schematic
    [FFB_Arduino_Yoke_1.0_Leonardo.fzz, FFB_Arduino_Yoke_1.1_Micro.fzz]
2022-12-21 Update Arduino.ino
    remove shift register definitions
2023-01-24 Change to IR Sensors, LCD update
    [Bearingblock.FCStd, Elektronik_V3.FCStd, FFB_Arduino_Yoke_1.1_Micro.fzz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]
2023-01-25 uplead schematic
2023-03-06 Version 1.3
    Version 1.3
    [BTS7960.FCStd, Back_Plate.FCStd, Backplate.FCStd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]
2023-03-08 Update Housing
    [Back_Plate.FCStd, Back_Plate.dxf, Bottom_Plate.FCStd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]
2023-03-13 Update Housing an Base Plate
    [Back_Plate.FCStd, Back_Plate.dxf, Bottom_Plate.FCStd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]
2023-03-21 Update Housing and Screws
    [LCD_Cover2.FCStd, Side_Plate.FCStd, Side_Plate_Left.FCStd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]
2023-03-22 Insert part list
2023-03-24 Update IR_Sensor_Pitch_Encoder model
    [IR_Sensor_Pitch_Encoder.FCStd]
2023-03-24 LCD wrong wire
2023-03-28 Bugfix Display, Serial Debug Forces
    [Arduino.ino, Communication.ino, Joystick.cpp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]
2023-04-21 Add Center Sensors
    Implement Sensors to detect the center position
    [IR_Sensor_Holder_Pitch_Center.FCStd, IR_Sensor_Holder_Roll_Center.FCStd, IR_Sensor_Pin_Pitch_Center.FCStd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]
2023-04-28 Make hole for sensor pin
    [IR_Sensor_Pin_Pitch_Center.FCStd, LinearGuide_Plate.FCStd]
2023-07-06 Insert PullUp Resistor
2024-08-21 Automatic Calibration
2024-09-02 Update Arduino.ino
    Update
2024-10-03 Add automatic calibration
2024-10-23 Update Schematic Image
2024-10-23 New Calibration, Beep Manager
2025-03-21 PCB Software 2.0
    PCB Software 2.0
    [BOM_FFB_Arduino_Yoke_2.0_YokeBoard.csv, BTS7960.FCStd, Back_Plate.FCStd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]
